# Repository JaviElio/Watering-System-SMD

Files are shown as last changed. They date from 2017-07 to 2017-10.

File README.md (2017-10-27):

# Watering-System-SMD

Watering system with Attiny84 and i2c moisture sensor.

THINGSPEAK LINK:

https://thingspeak.com/channels/339098

FEATURES:

 - Measures soil moisture, light and temperature.
 - It waters only at night.
 - It doesn't water if temperature is below 4ºC.
 - It waters depending on a preset value and a hysteresis.

 - It takes measurements every hour, then microcontroller goes to deep sleep.
 - If it irrigates, then checks moisture again after five minutes.
 - Measurements are uploaded to thingspeak.com

BILL OF MATERIALS:

 - Valve: https://www.aliexpress.com/item/Free-shipping-Plastic-solenoid-valve-12VDC-for-drink-water-air-6-35mm-1-4-Quick-plug/1411672083.html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
 
 - I2C Soil moisture sensor: https://www.tindie.com/products/miceuz/i2c-soil-moisture-sensor/?pt=full_prod_search
 
 - Enclosure: https://www.aliexpress.com/item/New-1-PC-Waterproof-115x90x55MM-Cover-Plastic-Electronic-Project-Box-Enclosure-Case-VE837-P0-3/32701644399.html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
 
 - Attiny84
 - MCP1703
 - 2N7000
 - AO3400
 - ESP-01

**TO IMPROVE**
 - Change protection diode with a schottky diode
 - Add a resistor in serial with diode D2 to close the EV slower
 - Connect the electrovalve and the diode D2 after the diode protection diode.

**PICTURES:**

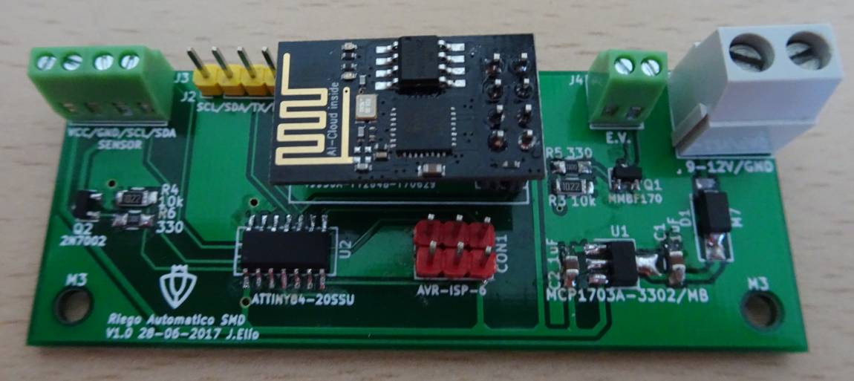
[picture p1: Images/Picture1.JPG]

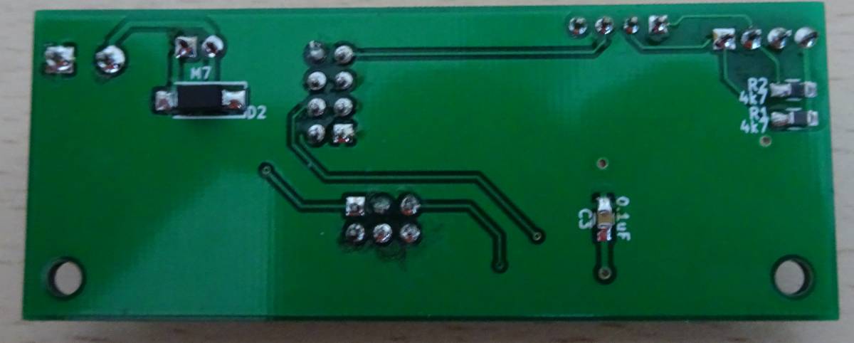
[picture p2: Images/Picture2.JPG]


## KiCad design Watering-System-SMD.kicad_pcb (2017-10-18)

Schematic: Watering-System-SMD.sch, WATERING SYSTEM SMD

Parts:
C1, C2: 1uF; C_0805_HandSoldering
C3: 0.1uF; C_0805_HandSoldering
CON1: AVR-ISP-6; Pin_Header_Straight_2x03_Pitch2.54mm
D1, D2: M7; D_SMA_Handsoldering
J1: Screw_Terminal_1x02; TerminalBlock_Pheonix_MKDS1.5-2pol
J2: CONN_01X04_MALE; Pin_Header_Straight_1x04_Pitch2.54mm
J3: Screw_Terminal_1x04; TerminalBlock_Pheonix_MPT-2.54mm_4pol
J4: Screw_Terminal_1x02; TerminalBlock_Pheonix_MPT-2.54mm_2pol
Q1: AO3400; SOT-23
Q2: 2N7002; SOT-23
R1, R2: 4k7; R_0805_HandSoldering
R3, R4: 10k; R_0805_HandSoldering
R5, R6: 330; R_0805_HandSoldering
U1: MCP1703A-3302/MB; SOT-89-3_Handsoldering
U2: ATTINY84-20SSU; SOIC-14_N
U3: ESP-01

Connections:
+12V: D1.2 (A), D2.1 (K), J1.2, J4.2
/CH_PD: U2.6 ((PCINT7/ICP/OC0B/ADC7)PA7), U3.6 (~CH_PD)
/EV_CONN: D2.2 (A), J4.1, Q1.3
/EV_ON: CON1.1, R3.2, R5.2, U2.8 ((PCINT5/DO/MISO/OC1B/ADC5)PA5)
/RST: CON1.5, U2.4 ((PCINT11/dW/~RESET~)PB3)
/RX: J2.3, U2.11 ((PCINT2/AIN1/ADC2)PA2), U3.4 (RXD)
/SCL: CON1.3, J2.1, J3.2, R2.1, U2.9 ((PCINT4/USCK/SCL/T1/ADC4)PA4)
/SDA: CON1.4, J2.2, J3.1, R1.1, U2.7 ((PCINT6/SDA/DI/MOSI/OC1A/ADC6)PA6)
/SENSOR_CONN: J3.3, Q2.3 (D)
/SENSOR_ON: R4.2, R6.2, U2.2 ((PCINT8/CLKI/XTAL1)PB0)
/TX: J2.4, U2.10 ((PCINT3/T0/ADC3)PA3), U3.5 (TXD)
GND: C1.2, C2.2, C3.2, CON1.6, J1.1, Q1.2, Q2.2 (S), R3.1, R4.1, U1.1 (GND), U2.14 (GND), U3.1 (GND)
unnamed: C1.1, D1.1 (K), U1.2 (VI)
unnamed: Q1.1, R5.1
unnamed: Q2.1 (G), R6.1
VCC: C2.1, C3.1, CON1.2, J3.4, R1.2, R2.2, U1.3 (VO), U2.1 (VCC), U3.7 (~RST), U3.8 (VCC)

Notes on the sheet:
V. Regulator
Connections
I2C
WIFI
Transistors

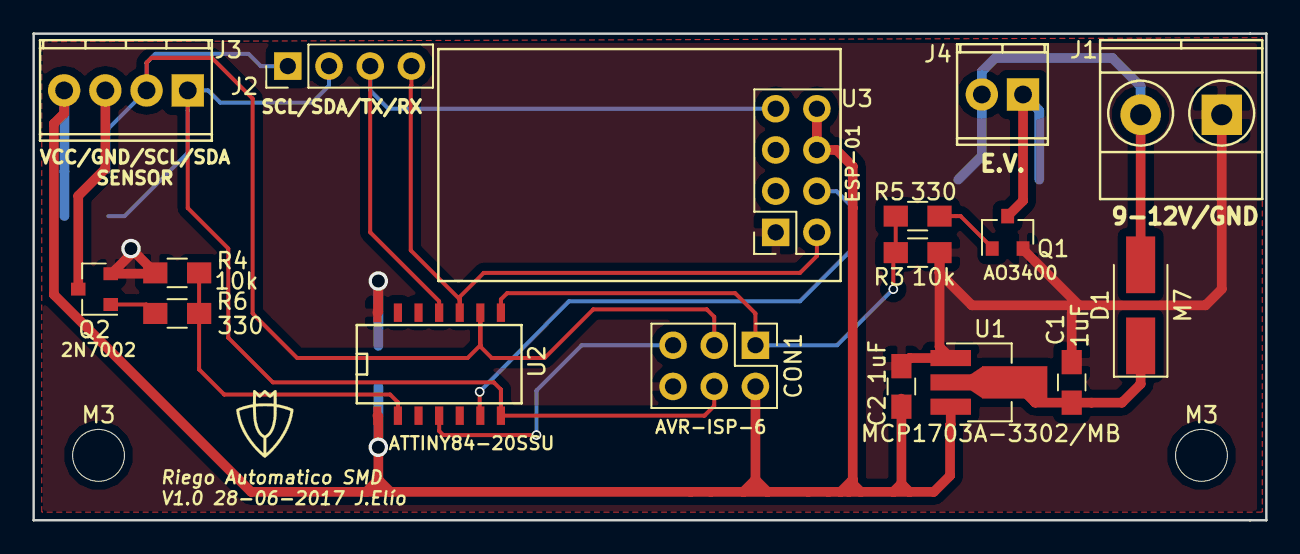
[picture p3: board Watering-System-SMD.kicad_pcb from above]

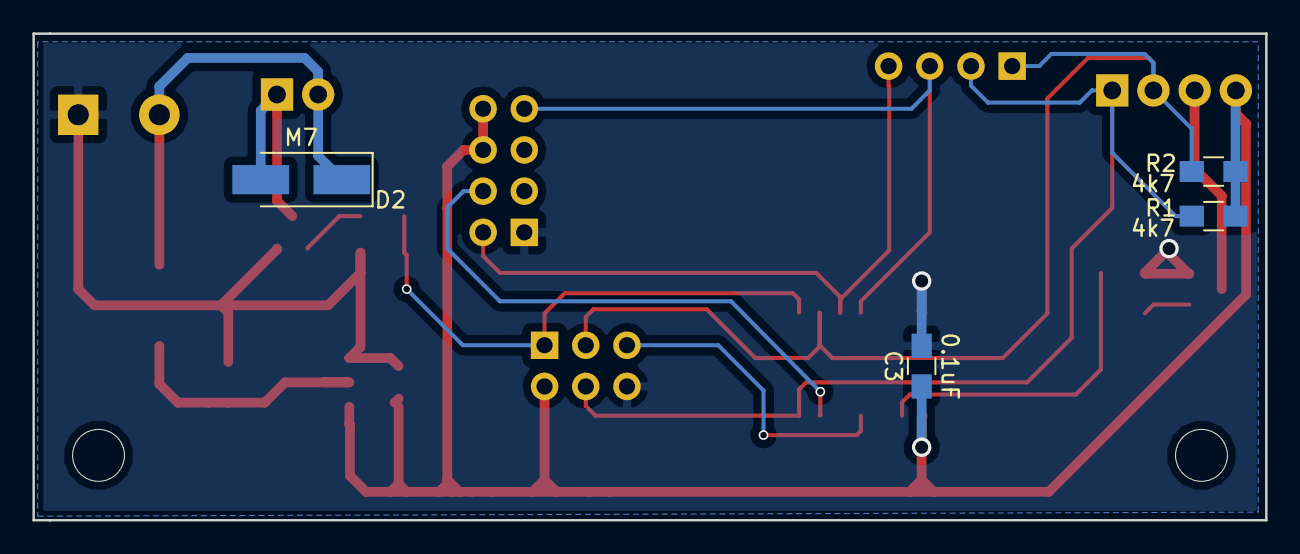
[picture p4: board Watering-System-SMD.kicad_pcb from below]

Board: 2 copper layers, 76.0 x 30.0 mm, 23 parts (4 on the bottom side), 16 nets.

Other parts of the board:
M3, M3#2: MountingHole_3.2mm_M3

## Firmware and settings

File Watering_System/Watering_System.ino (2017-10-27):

/**********************************************
  Project: Watering System SMD V1.0       31-07-2017
  JEC
***********************************************
***********************************************
 
 Comments:
  - ESP-01 must be previously configured:
      * AT+CWMODE_DEF=3                         // SoftAP+Station mode 
      * AT+CWJAP_DEF= "<ssid>","<password>"     // Connect to wifi access point
      * AT+UART_DEF=9600,8,1,0,0                // Set UART speed to 9600
      
************************************************/

// INCLUDES
#include <I2CSoilMoistureSensor.h>
#include <TinyWireM.h>
#include <SoftwareSerial.h>
#include <avr/pgmspace.h>
#include <avr/sleep.h>
#include <avr/wdt.h>
#include <avr/interrupt.h>


// ADJUSTMENT VARIABLES
unsigned int nLightMax         = 40000;           // Max light to water
unsigned int nTempMin          = 4;               // Min. temp to water (ºC)
unsigned int nMoistureMin      = 490;             // Min. moist to water
unsigned int nMoistureMax      = 540;             // Max. moist to water
unsigned int nWateringTime     = 20000;           // Watering time (ms) 
unsigned int nMaxWateringTimes = 5;               // Max. watering times




// DEFINES
#define EV_ON       PORTA |=  (1 << PORTA5)
#define EV_OFF      PORTA &= ~(1 << PORTA5)

#define SENSOR_ON   PORTB |=  (1 << PORTB0)
#define SENSOR_OFF  PORTB &= ~(1 << PORTB0)

#define ESP_ON      PORTA |=  (1 << PORTA7)
#define ESP_OFF     PORTA &= ~(1 << PORTA7)
#define RX          PORTA3
#define TX          PORTA2
#define BAUDRATE    9600

//#define IP          "184.106.153.149"           // thingspeak.com




// OBJECTS
I2CSoilMoistureSensor sensor(0x20);
SoftwareSerial esp(RX, TX);
//SoftwareSerial debug(-1, PORTA4);

// VARIABLES
int          nState = 0;
const char*  GET = "GET /update?key=XXXXXXXXXXXXXX&field1=%u&field2=%d&field3=%d&field4=%d";
char         cmd[80];
int          nChars = 0;
uint16_t     nLight;                      // Measured light value
int          nTemp;                       // Measured temp value
unsigned int nMoisture;                   // Measured moist value
unsigned int nShortSleep = 300;           // Short sleep lenght in seconds 300s=5min
unsigned int nLongSleep = 3600;           // Long sleep lenght in seconds 3600s=1h
bool         bOldState = 0;               // Previous valve state
unsigned int nWateringTimes = 0;          // Watering times





void setup() {

  configurePins();
  setupPowerSaving();
  esp.begin(BAUDRATE);        // Init serial comm.
  TinyWireM.begin();          // Init i2c comm.

}


void loop() {

  switch (nState) {

          case 0:   // Switch on sensor

                SENSOR_ON;
                delay(1500);
                nState = 10;
                break;
                

          case 10:  // Measure light, temperature and moisture
                
                nLight = sensor.getLight(true);
                nTemp = sensor.getTemperature()/10;
                nMoisture = sensor.getCapacitance();
                SENSOR_OFF;                             // Switch off sensor
       
          
                // If "dark" and tempeture is higher that min then water
                if ((nLight > nLightMax) && nTemp > nTempMin) {
                  nState = 20;
                }
          
                // No watering then go to sleep
                else {
                  
                  nWateringTimes = 0;
                  bOldState = false;
                  nState = 200;
                  
                }

       
                break;

           case 20: // Check moist
        
        
        
              if ((nMoisture < nMoistureMin) || (nMoisture < nMoistureMax) && bOldState) {
        
                nWateringTimes++;
        
                if (nWateringTimes > nMaxWateringTimes) {
                  nWateringTimes = 0;
                  bOldState = false;
                  nState = 200;
                }
                else {
                  bOldState = true;
                  nState = 30;
                }
              }
        
              if ((nMoisture > nMoistureMax) || (nMoisture > nMoistureMin) && !bOldState) {
        
                nWateringTimes = 0;
                bOldState = false;
                nState = 200;
              }


                break;    



          case 30:  // Water


                EV_ON;                    // Switch on solenoid valve
                delay(nWateringTime);     // Watering................
                EV_OFF;                   // Switch off solenoid valve

                nState = 100;
                break;

          case 100:   // Short sleep

                uploadData();                           // Send data to thinkspeak.com
                sleep(nShortSleep/8);                       // Sleep "nShortSleep" seconds
                nState = 0;
                break;
      
          case 200:   // Long sleep
      
                uploadData();                           // Send data to thinkspeak.com
                sleep(nLongSleep/8);                        // Sleep "nLongSleep" seconds
                nState = 0;
                break;
      
      
          default: nState = 0;




  }

  
}

/*
bool espCommand ( char* input, char* output, uint8_t length, unsigned int timeout, unsigned int maxAttempts) {

                unsigned int attempts = 0;
  
                 while (attempts < maxAttempts) {
                  
                      clearBuffer();
                      esp.println(input);
            
                      if (waitForString(output,length,timeout)) {
                          return true;
                      }
                      else {
                          attempts++;
                          //debug.println();
                          //debug.println(attempts,DEC);
                      }
                                       
                }

                return false;
}






bool waitForString(char* input, uint8_t length, unsigned int timeout) {

  unsigned long end_time = millis() + timeout;
  int current_byte = 0;
  uint8_t index = 0;

  while (end_time >= millis()) {

    if (esp.available()) {

      //Read one byte from serial port
      current_byte = esp.read();
      //debug.print(char(current_byte));

      if (current_byte != -1) {
        //Search one character at a time
        if (current_byte == input[index]) {
          index++;

          //Found the string
          if (index == length) {
            return true;
          }
          //Restart position of character to look for
        } else {
          index = 0;
        }
      }
    }
  }
  //Timed out

  return false;
}



//Remove all bytes from the buffer
void clearBuffer() {

  while (esp.available())
    esp.read();
}

*/


//Count bytes in a char string
uint8_t countChars(char* inputChar) {

    uint8_t n = 0;
    
    while (inputChar[n]!= 0) {
      //debug.print(inputChar[n]);
      n++;
    }
  
  //debug.println();
  return n+2;
}


void configurePins() {
  
  DDRB |= (1 << DDB0);      // B0 -> Output (SENSOR ON)
  DDRA |= (1 << DDA7);      // A7 -> Output (PWR ESP)
  DDRA |= (1 << DDA5);      // A5 -> Output (E.VALVE)

  
}




void uploadData() {


      // Switch on ESP and wait while connects to wifi network
      ESP_ON;
      delay(10000);

      // Connect to thinkspeak.com
      esp.println(F("AT+CIPSTART=\"TCP\",\"184.106.153.149\",80"));
      delay(1000);

      // Write command in "cmd"
      sprintf(cmd,GET,nLight,nTemp,nMoisture, bOldState);
      nChars = countChars(cmd);

      // Send command
      esp.print(F("AT+CIPSEND="));
      esp.print(nChars);
      esp.println();
      delay(1000);
      esp.println(cmd);
      delay(1500);
      ESP_OFF; 
  
}

void setupWatchdog() {
  cli();                                            // Disable global interrupts
  // Set watchdog timer in interrupt mode
  // allow changes, disable reset
  WDTCSR = bit (WDCE) | bit (WDE);
  // set interrupt mode and an interval
  WDTCSR = bit (WDIE) | bit (WDP3) | bit (WDP0);     // set WDIE, and 8 seconds delay
  sei();                                            // Enable global interrupts
}


void sleep(int times) {

  setupWatchdog();                                  // Configure and activate Watchdog

  for (int i = 0; i < times; i++) {

    cli();                                          // Disable interruptions just in case
    sleep_enable();                                 // Enable sleep


    //    sleep_bod_disable();                       // Deshabilitar BOD durante sleep
    //    MCUCR |= _BV(BODS) | _BV(BODSE);           //disable brownout detection during sleep
    //    MCUCR &=~ _BV(BODSE);

    sei();                                          // Enable interruptions
    sleep_cpu();                                    // Go to sleep
    sleep_disable();                                // When cpu is awake, disable sleep

  }

  wdt_disable();                                    // Disable watchdog in order to not have more WDT interruptions
}


void setupPowerSaving() {

  ADCSRA &= ~(1 << ADEN);                           // Disable ADC
  set_sleep_mode(SLEEP_MODE_PWR_DOWN);              // Configure sleep mode
  
}

ISR(WDT_vect) {

  // Nothing to do, just wake up

}

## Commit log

2017-05-22 Initial upload
    [Watering-System-SMD.kicad_pcb, Watering-System-SMD.sch]
2017-06-15 ESP-01 added
    [Watering-System-SMD.kicad_pcb, Watering-System-SMD.sch]
2017-06-17 PCB routed
    [Watering-System-SMD.kicad_pcb, Watering-System-SMD.sch]
2017-06-17 SilkScreen changed
    [Watering-System-SMD.kicad_pcb, Watering-System-SMD.sch]
2017-06-19 gerber folder uploaded
    [Watering-System-SMD-B.Cu.gbr, Watering-System-SMD-B.Mask.gbr, Watering-System-SMD-B.SilkS.gbr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]
2017-06-20 logo added to silkscreen
    [Watering-System-SMD.kicad_pcb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]
2017-06-28 CH-PD routed
    [Watering-System-SMD-B.Cu.gbr, Watering-System-SMD-B.Mask.gbr, Watering-System-SMD-B.SilkS.gbr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]
2017-06-28 date changed
    [Watering-System-SMD.kicad_pcb]
2017-06-28 gerbers uploaded
    [Watering-System-SMD-B.Cu.gbr, Watering-System-SMD-B.Mask.gbr, Watering-System-SMD-B.SilkS.gbr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]
2017-08-27 First working version. It measure temperature, moisture, and light. Waters depending on this measurements and then sleeps.
2017-10-18 MOSFET transistor changed
    [Watering-System-SMD.sch]
2017-10-18 MOSFET changed
    [Watering-System-SMD.kicad_pcb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]
